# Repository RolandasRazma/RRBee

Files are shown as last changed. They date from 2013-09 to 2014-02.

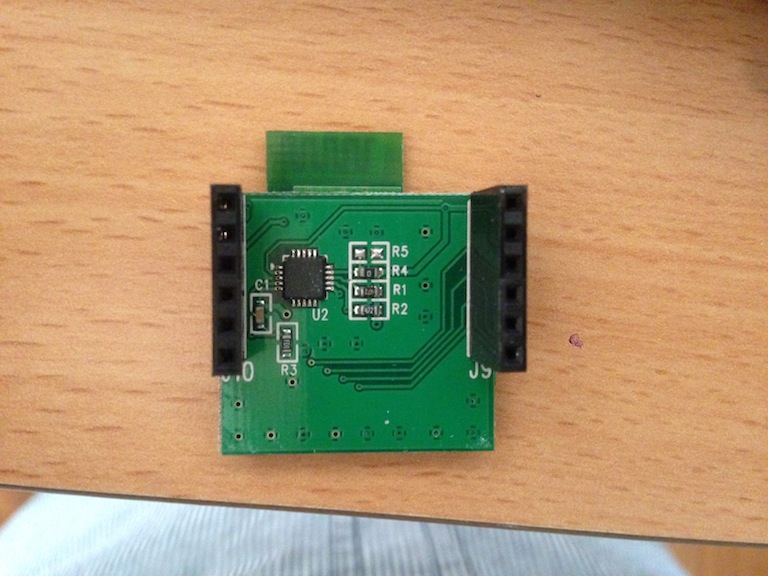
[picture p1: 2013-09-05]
Hardware/Car/bluetooth_breakout_board_back_side.jpg

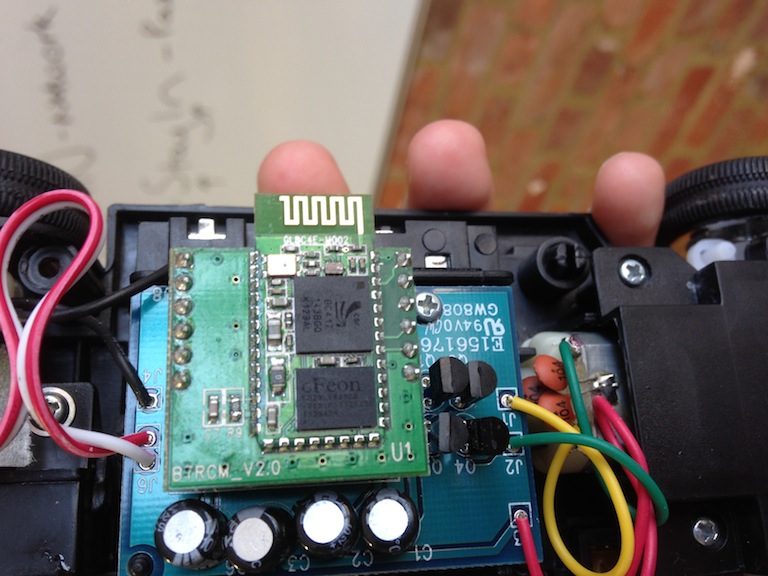
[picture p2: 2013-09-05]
Hardware/Car/bluetooth_receiver.jpg

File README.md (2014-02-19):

RRBee
=====

Pet project for [BeeWi Mini Cooper](http://www.bee-wi.com/bluetooth-controlled-car,us,4,BBZ251-A6.cfm) controlling [@YPlan](http://yplanapp.com)<br />

BeeWi Mini Cooper [@YPlan](http://yplanapp.com)
------

It's not interesting when it's only work and no pleasure, so we got a [BeeWi Mini Cooper](http://www.bee-wi.com/bluetooth-controlled-car,us,4,BBZ251-A6.cfm) [@YPlan](http://yplanapp.com) to shorten those "hard" days :)<br />
BeeWi Mini Cooper<br />
It's a nice toy, and best of all - it is [Bluetooth](http://en.wikipedia.org/wiki/Bluetooth) controlled over iPhone! All you need is free [iOS application](https://itunes.apple.com/gb/app/beewi-control-pad/id427936738?mt=8). After few [drag races](http://en.wikipedia.org/wiki/Drag_racing) with our designer [João Pires](https://twitter.com/joaorafaelpires) we started to chat how it would be cool to mod it. You know... like add blinking lights, WiFi camera and etc, and best of all - I can write iOS application to do all that!<br />

Modding BeeWi Mini Cooper [@YPlan](http://yplanapp.com)
------

First of all I had to figure out how to send signals to [BeeWi Mini Cooper](http://www.bee-wi.com/bluetooth-controlled-car,us,4,BBZ251-A6.cfm) over Bluetooth. Apparently it's quite simple. You just need to add `UISupportedExternalAccessoryProtocols` to `Info.plist` and connect to it using [ExternalAccessory.framework](https://developer.apple.com/library/ios/documentation/ExternalAccessory/Reference/ExternalAccessoryFrameworkReference/_index.html). I got `UISupportedExternalAccessoryProtocols` from [official App](https://itunes.apple.com/gb/app/beewi-control-pad/id427936738?mt=8) by extracting <a href="http://en.wikipedia.org/wiki/.ipa_(file_extension)">IPA</a> and poking in their own `Info.plist`. I was about to start sniff Bluetooth data by emulating car, to check what data comes in to control it, but surprisingly found another project on GitHub that already did that [@hdi-95 hdi-remotepad](https://github.com/hdi-95/hdi-remotepad). That was pretty simple. Apparently you need only 8 command `0`-`7`. <br />
  * `0` - Stop go forward
  * `1` - Go forward
  * `2` - Stop go backwards
  * `3` - Go backwards
  * `4` - Stop turn Left
  * `5` - Turn Left
  * `6` - Stop Turn Right
  * `7` - Turn Right

You can clone <a href="https://github.com/RolandasRazma/RRBee/tree/master/iOS%20App%20(Default)">my basic iOS app</a> to control BeeWi!<br />

BeeWi Mini Cooper - Hardware
------
Ok. So I need more of those signals to turn on and off lights. Disassembling is quite easy. There is only 4 screws at the bottom. <br />
4 screws<br />

Lets inspect whats under the hood. What you see standard Bluetooth receiver on [breakout board](http://en.wikipedia.org/wiki/Breakout_board), and very simple [PCB](http://en.wikipedia.org/wiki/Printed_circuit_board) under it.<br />
chassi
chassis without Bluetooth receiver
PCB back side
Bluetooth receiver
Bluetooth breakout board <br />

Ok, so we have Bluetooth serial communication module (most likely cheap one) and [breakout board](http://en.wikipedia.org/wiki/Breakout_board) with [micro controller](http://en.wikipedia.org/wiki/Micro_controller). I fast checked all 8 pins on breakout board using [multimeter](http://en.wikipedia.org/wiki/Multimeter) and unfortunately only 4 of those are for serial signal, other 4 are for [ISP](http://en.wikipedia.org/wiki/In-system_programming), 2 for ground, 1 for Vcc, and 1 unused for [LED](http://en.wikipedia.org/wiki/Led).<br />

4 pins only... `Go forward`, `Go backwards`, `Turn Left`, `Turn Right`… Clearly no place for all cool features I would like to add... even worser - after some experiments I figured out that __only 2__ of them can be active at the same time (for example `1` go forward + `7` turn right) so there is no way I could do some logic with [gates](http://en.wikipedia.org/wiki/Logic_gate)...<br />

Bluetooth breakout board pins<br />

BeeWi Mini Cooper - Modding Hardware
------
So my choices pretty narrow here:
  * figure out what micro controller is used on breakout board and try to reprogram it.
  * cut micro controller from breakout board and add new one with enough pins I could program.
  * use [Shift register](http://en.wikipedia.org/wiki/Shift_register) to increase number of available outputs.<br />
  
*__What is Shift Registers?__*<br />
[Shift register](http://en.wikipedia.org/wiki/Shift_register) in principle it is "device" that counts how many impulses you gave to it. Every time you give impulse it shifts bit by one position. If you had `00000000` (look at legs of it) after you "give it" `1` it will have value of `00000001`, if you then "give it" `0` and `1` again, it will have value of `00000101`. It is very simple to operate, you can connect them in <a href="http://en.wikipedia.org/wiki/Daisy_chain_(electrical_engineering)">daisy chain</a> to get virtually unlimited number of outputs and best of all you need only 3-4 wires to do so.<br /><br />
Depending on Shift register model it might have different pins, but for [74HC595 Shift Register](http://www.nxp.com/documents/data_sheet/74HC_HCT595.pdf) they are as follow:
 * `1` - output (QB)
 * `2` - output (QC)
 * `3` - output (QD)
 * `4` - output (QE)
 * `5` - output (QF)
 * `6` - output (QG)
 * `7` - output (QH)
 * `8` - <a href="http://en.wikipedia.org/wiki/Ground_(electricity)">GND</a> - ground pin you connecting to `-` of your [power supply](http://en.wikipedia.org/wiki/Power_supply)
 * `9` - output used for connecting several shift register together (QH')
 * `10` - serial clear - Will clear all values if no current is given. Most of the time you want it to be connected to power supply `+`
 * `11` - serial clock - When this pin is pulled high (has current), it will shift the register to whatever value is given on pin `14`
 * `12` - register clock - After you set value you want (by operating pin `11` and pin `14`) this pin needs to be pulled high (have current) to set the output to the new values. It must be pulled high after serial clock (pin `11`) has gone LOW.
 * `13` - output enabled - enables output when tied to ground (power supply `-`). If you want to temporary disable output without affecting shift register value you can pull it HIGH
 * `14` - serial input - value for the next bit that gets shifted in (when pin `11` is HIGH)
 * `15` - output (QA)
 * `16` - <a href="http://en.wikipedia.org/wiki/IC_power_supply_pin">VCC</a> - `+` of your power supply



<br />

*__Wireing__*<br />
I thought that [Shift registers](http://en.wikipedia.org/wiki/Shift_register) is simplest solution as you can get virtually unlimited outputs, it would move all logic to software (iOS app) and most important in my case is that I can control it with 3 wires (remember that BeeWi Bluetooth breakout board has only 4 and allows only 2 be active at same time)

I had couple of [74HC595 Shift Registers](http://www.nxp.com/documents/data_sheet/74HC_HCT595.pdf) lying around as they are pretty common so I decide to hook it up.

Before I start soldering everything to BeeWi PCB I have to test if it would work. I started putting everything on [Breadboard](http://en.wikipedia.org/wiki/Breadboard). First, Bluetooth breakout board from BeeWi and Shift register, then added simple [power supply](http://en.wikipedia.org/wiki/Power_supply) I had and some [LED](http://en.wikipedia.org/wiki/Light-emitting_diode)'s. Then wrote simple <a href="https://github.com/RolandasRazma/RRBee/tree/master/iOS%20App%20(Mod)">iOS app</a> to set bits as I wanted. Good, now I have 8 independant outputs!

Breadboard, BeeWi Bluetooth pins, Shift register, LEDs, Transistor, Resistor
Breadboard, BeeWi Bluetooth pins, Shift register, LEDs, Transistor, Resistor, Control jumpers
Breadboard, BeeWi Bluetooth pins, Shift register, LEDs, Transistor, Resistor, Jumpers
Breadboard, BeeWi Bluetooth pins, Shift register, LEDs, Transistor, Resistor, Jumpers - assembled, on
Breadboard<br />

*__Putting back together__*<br />
It's time to put all back together. There is no place for shift register on bottom of original PCB so I decided to put it on the top. First of all I needed to cut old connections going to Bluetooth breakout board as they will be replaced with new ones driven by shift register. It's not that hard if you have [crafts knife](http://www.google.com/search?q=crafts+knife&tbm=isch). <br />




`to be continued...`

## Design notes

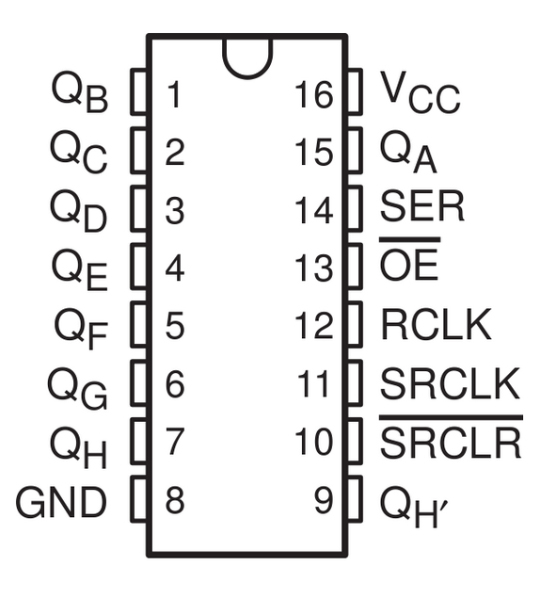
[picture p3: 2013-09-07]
Hardware/74HC595/74HC595_pinout.jpg

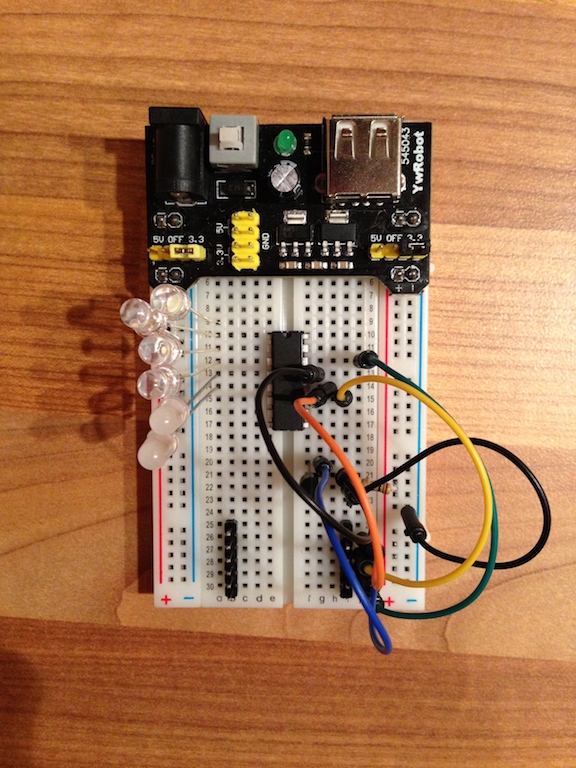
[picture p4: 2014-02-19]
Hardware/Breakout/breadboard_bt_74HC595_LEDs_transistor_resistor_control_jumpers.jpg

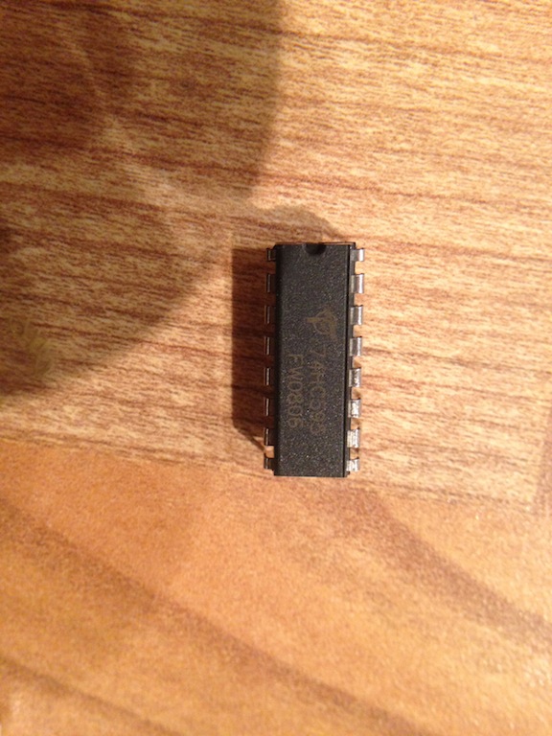
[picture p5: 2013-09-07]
Hardware/74HC595/74HC595.jpg

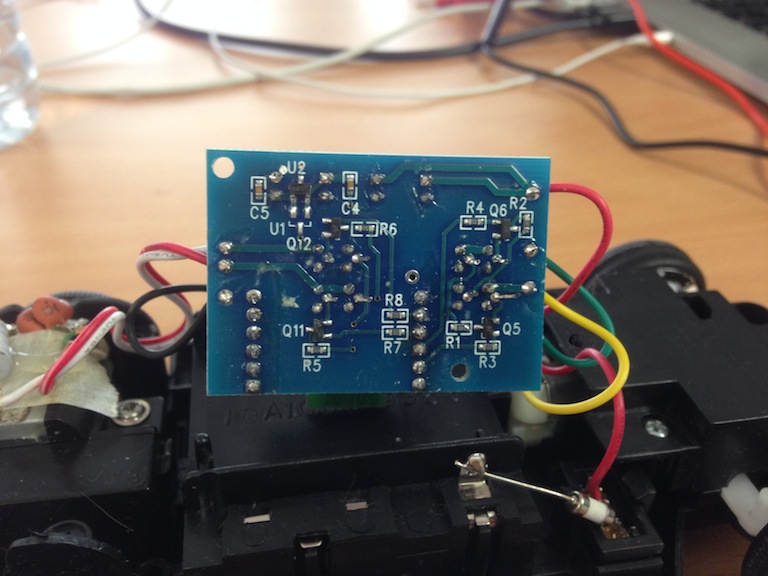
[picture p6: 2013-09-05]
Hardware/Car/pcb_other_side.jpg

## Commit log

2013-09-08 added schematics
    [breadboard_components.fzz]
2014-02-19 updated images and describtions to show resistor and transistor
    [breadboard_components.fzz]
